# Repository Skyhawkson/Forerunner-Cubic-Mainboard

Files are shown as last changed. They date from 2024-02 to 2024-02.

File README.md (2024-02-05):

# Forerunner-Cubic-Mainboard
**NOTE:** Development prior to Rev1.0.1 occurred in a seperate repository

Forerunner-Cubic-Mainboard-enclosed

Forerunner Cubic is a small form-factor (55 x 55 x ~70mm) flight controller for high-powered rockets and my personal UAV projects. The mainboard uses an ESP32 WROOM-32D module for a processor, and handles data storage, USB, and Single-Pair Ethernet communication with other future devices. The stacking headers enable a connection to other boards handling:
- RF Communication and Control
- Inertial, air data, and environmental sensors
- Servo and pyrotechnic control
- Battery management and power distribution

Design information is available in the [Schematic](https://github.com/Skyhawkson/Forerunner-Cubic-Mainboard/blob/main/Forerunner%20Cubic%20Mainboard%20Rev1.0.1/Forerunner-Cubic-Mainboard.pdf) as well as the [KiCAD 7 Project File](https://github.com/Skyhawkson/Forerunner-Cubic-Mainboard/tree/main/Forerunner%20Cubic%20Mainboard%20Rev1.0.1/Forerunner-Cubic-Mainboard-Rev1.0.1)

The PCB's outer dimensions measure 50 x 50mm, in order to fit within a standard 3" body tube. 

Forerunner_Cubic_PCB

Forerunner_Cubic_Tube

**Board Images:**

Forerunner_Cubic_Bottom
Forerunner_Cubic_Top

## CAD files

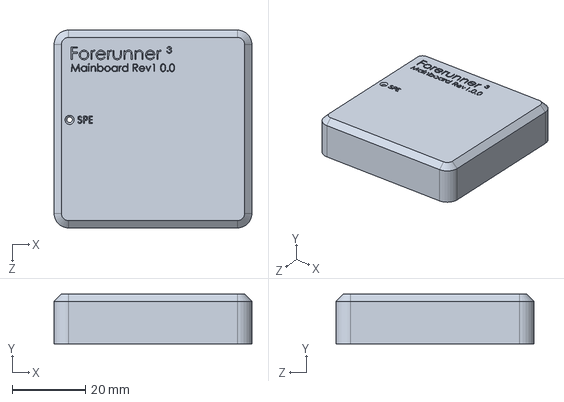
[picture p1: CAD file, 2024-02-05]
Forerunner Cubic Mainboard Rev1.0.1/Bench Test Enclosure/Case Top.SLDPRT
54.0 x 13.6 x 54.0 mm

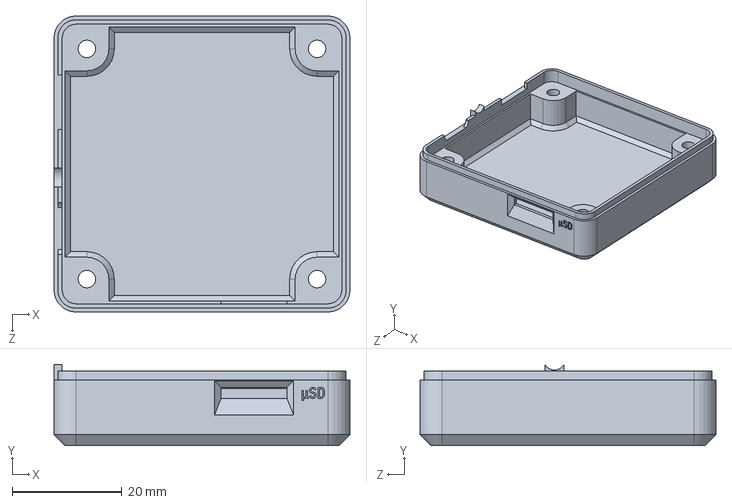
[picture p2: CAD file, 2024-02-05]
Forerunner Cubic Mainboard Rev1.0.1/Bench Test Enclosure/Case Bottom.SLDPRT
54.0 x 14.8 x 54.0 mm

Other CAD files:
Forerunner Cubic Mainboard Rev1.0.1/Bench Test Enclosure/Case Bottom.STL
Forerunner Cubic Mainboard Rev1.0.1/Bench Test Enclosure/Case Top.STL

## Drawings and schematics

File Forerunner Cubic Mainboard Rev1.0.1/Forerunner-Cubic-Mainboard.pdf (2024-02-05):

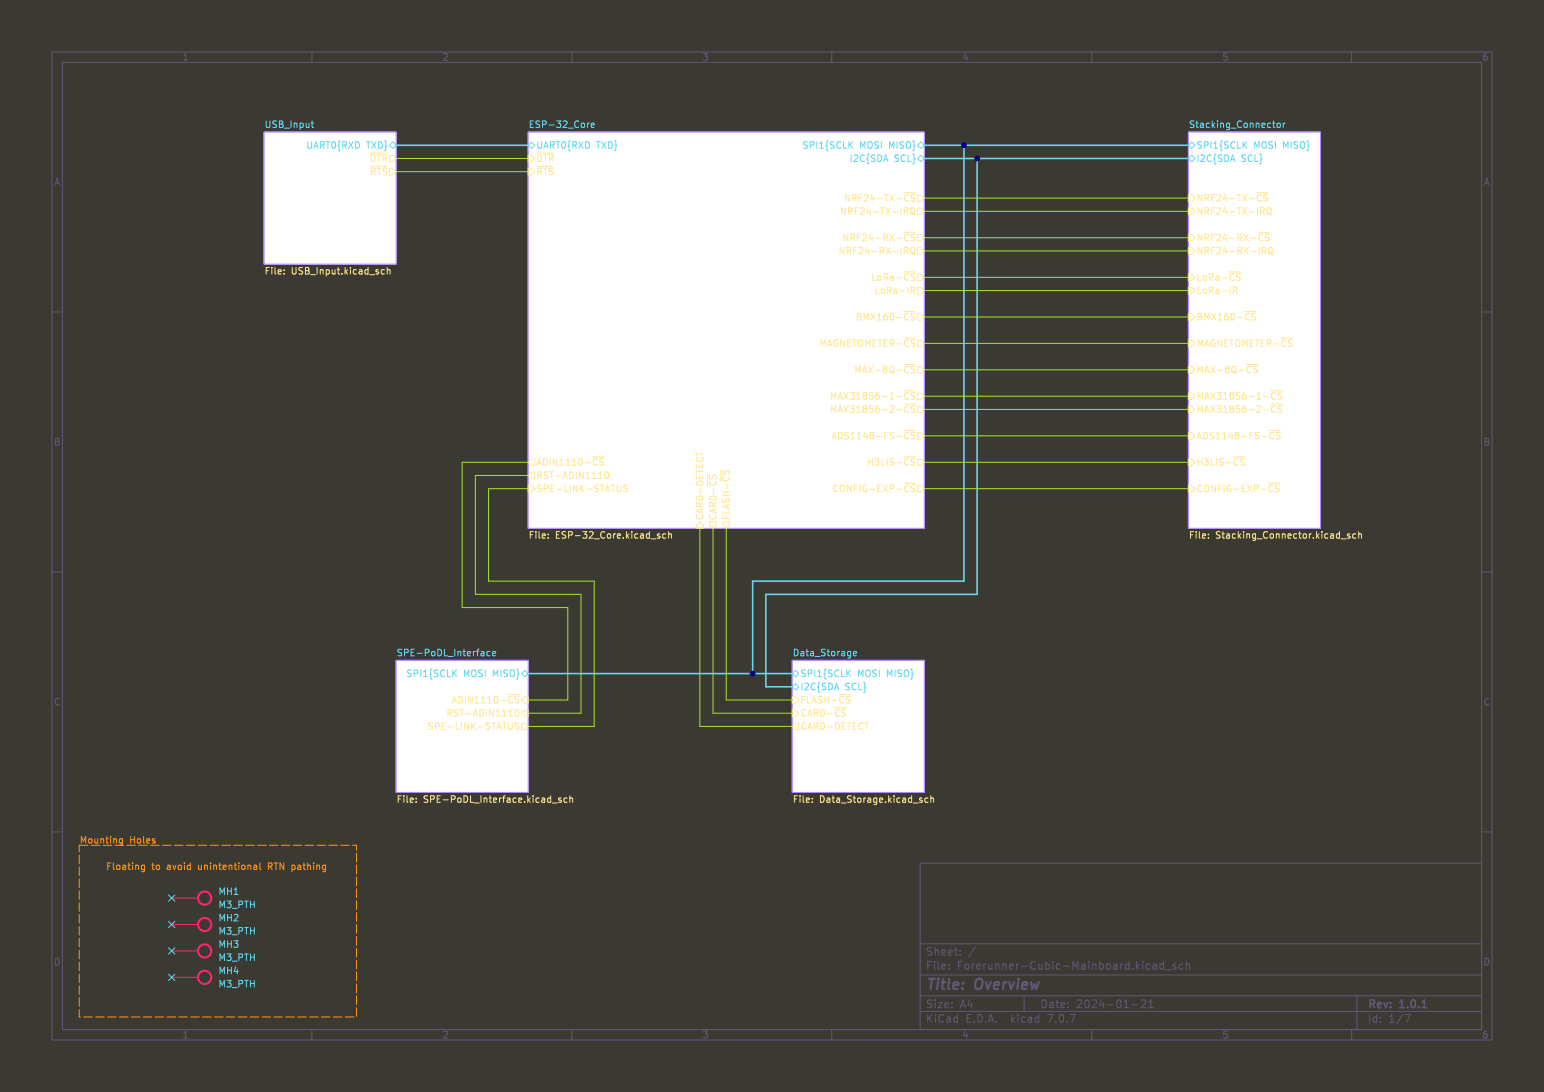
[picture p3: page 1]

NRF24-TX-~{CS} NRF24-RX-IRQ
LoRa-~{CS} NRF24-TX-IRQ

ADIN1110-~{CS} SPE-PoDL_Interface File: SPE-PoDL_Interface.kicad_sch
File: Forerunner-Cubic-Mainboard.kicad_sch Sheet: / SPI1{SCLK MOSI MISO} RST-ADIN1110 SPE-LINK-STATUS

SPI1{SCLK MOSI MISO} CARD-DETECT
I2C{SDA SCL}
FLASH-~{CS}
CARD-~{CS}

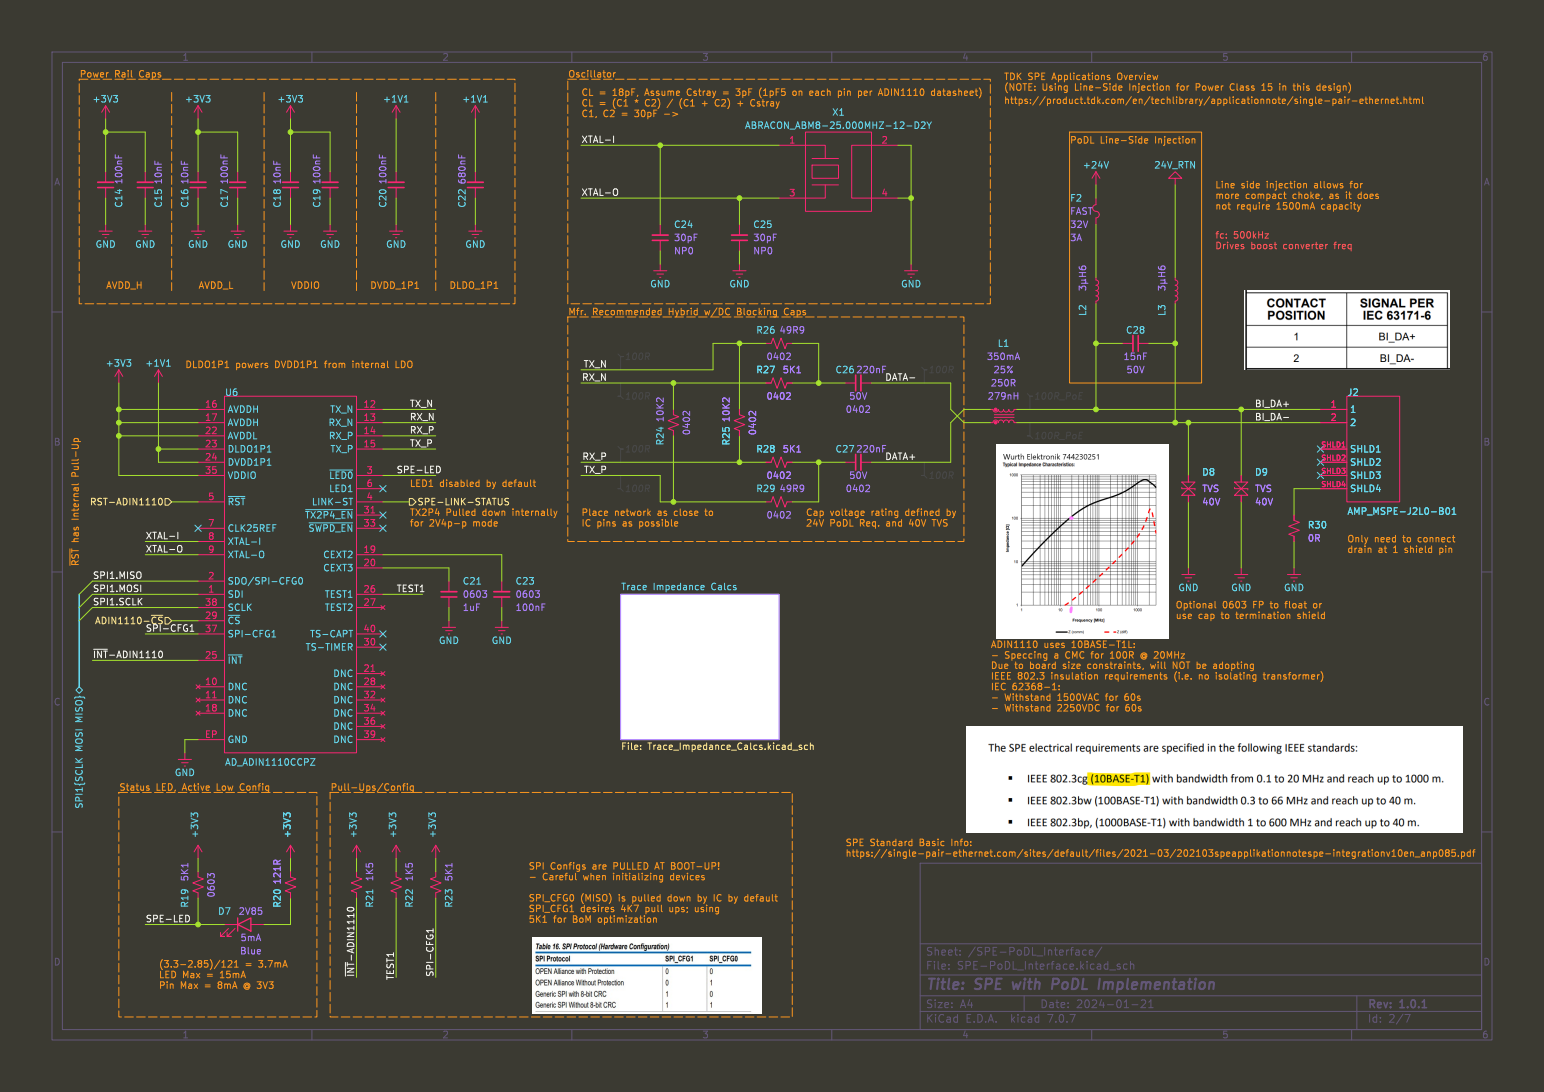
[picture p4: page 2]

Id: 2/7 Title: SPE with PoDL Implementation

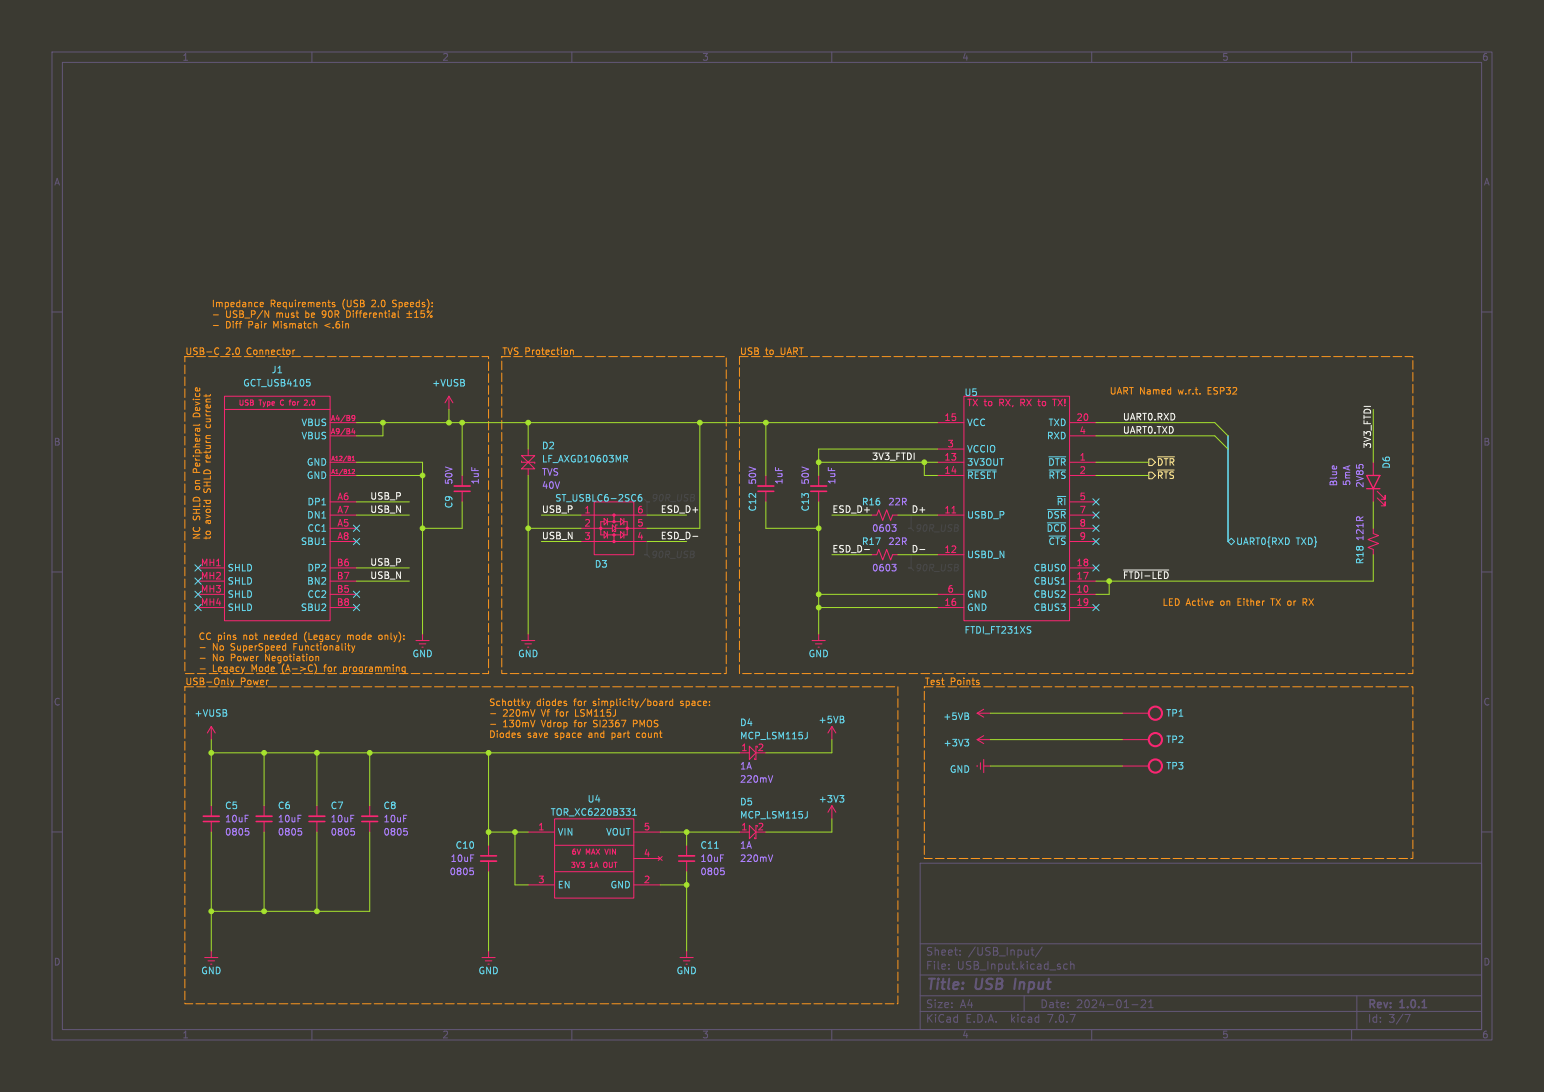
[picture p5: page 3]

Id: 3/7 Title: USB Input File: USB_Input.kicad_sch Sheet: /USB_Input/ R16

- 130mV Vdrop for SI2367 PMOS Diodes save space and part count CC pins not needed (Legacy mode only): - No SuperSpeed Functionality

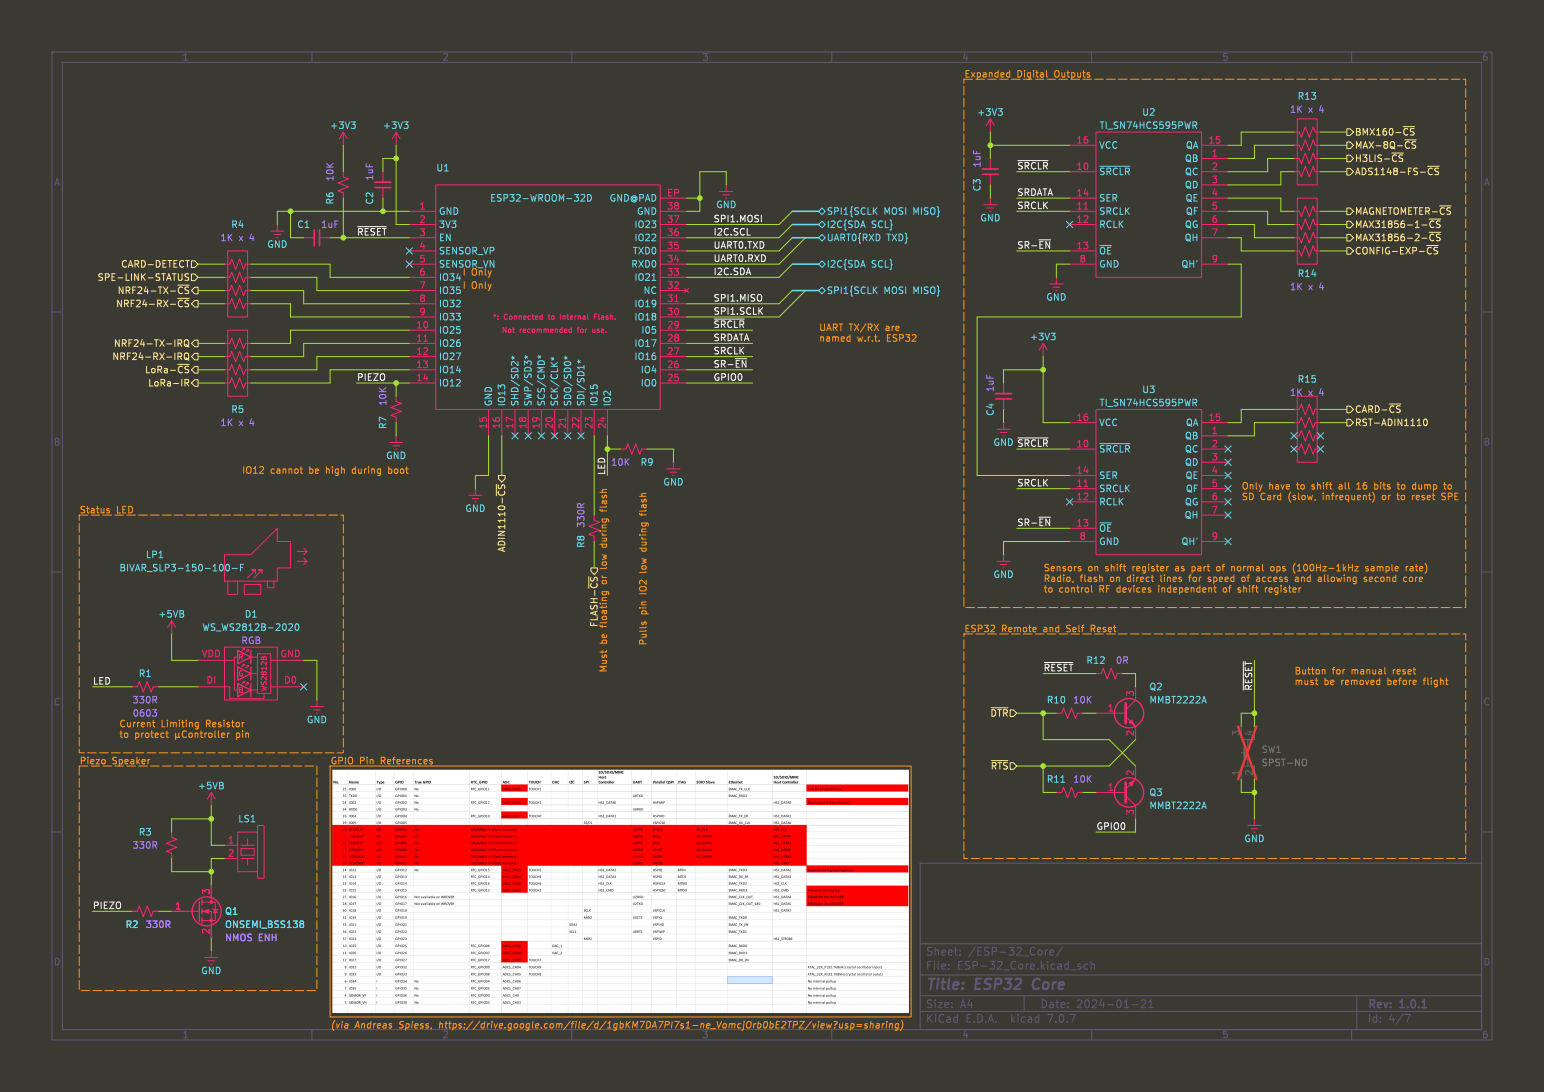
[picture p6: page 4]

CONFIG-EXP-~{CS} FLASH-~{CS}

CARD-DETECT
NRF24-RX-~{CS} SPE-LINK-STATUS NRF24-TX-IRQ
NRF24-TX-~{CS} NRF24-RX-IRQ

(via Andreas Spiess, https://drive.google.com/file/d/1gbKM7DA7PI7s1-ne_VomcjOrb0bE2TPZ/view?usp=sharing) Q1 ONSEMI_BSS138 NMOS ENH

File: ESP-32_Core.kicad_sch Sheet: /ESP-32_Core/
Id: 4/7 Title: ESP32 Core

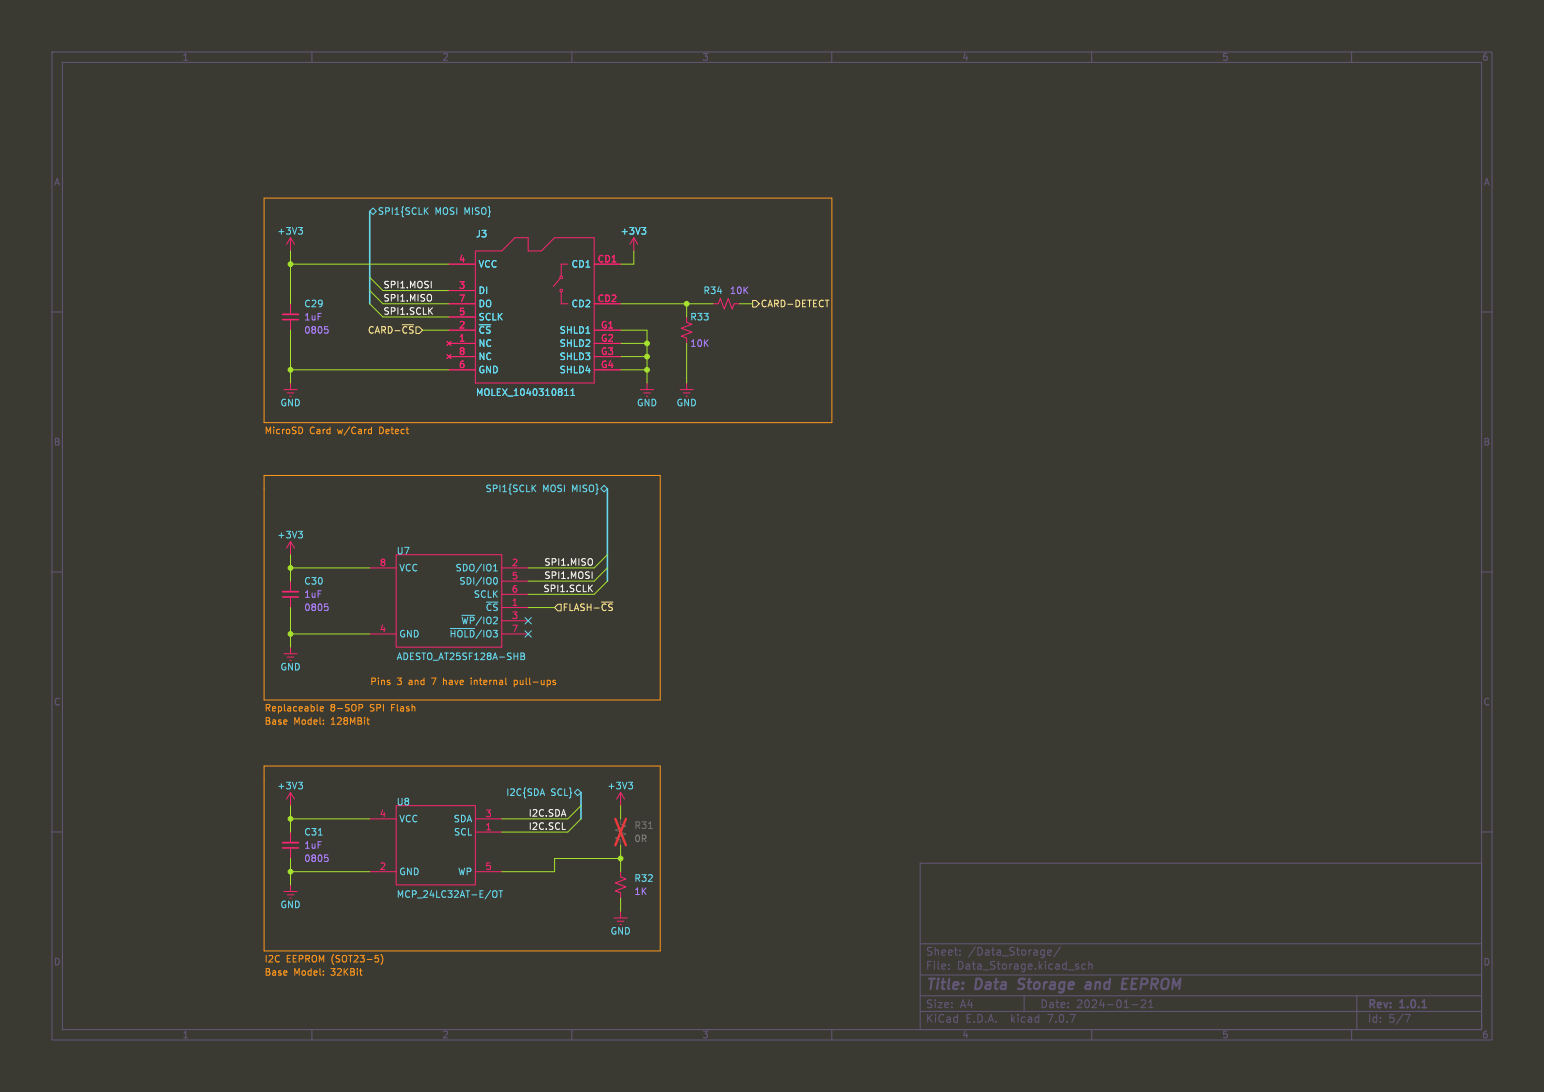
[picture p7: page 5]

File: Data_Storage.kicad_sch Sheet: /Data_Storage/
Id: 5/7 Title: Data Storage and EEPROM

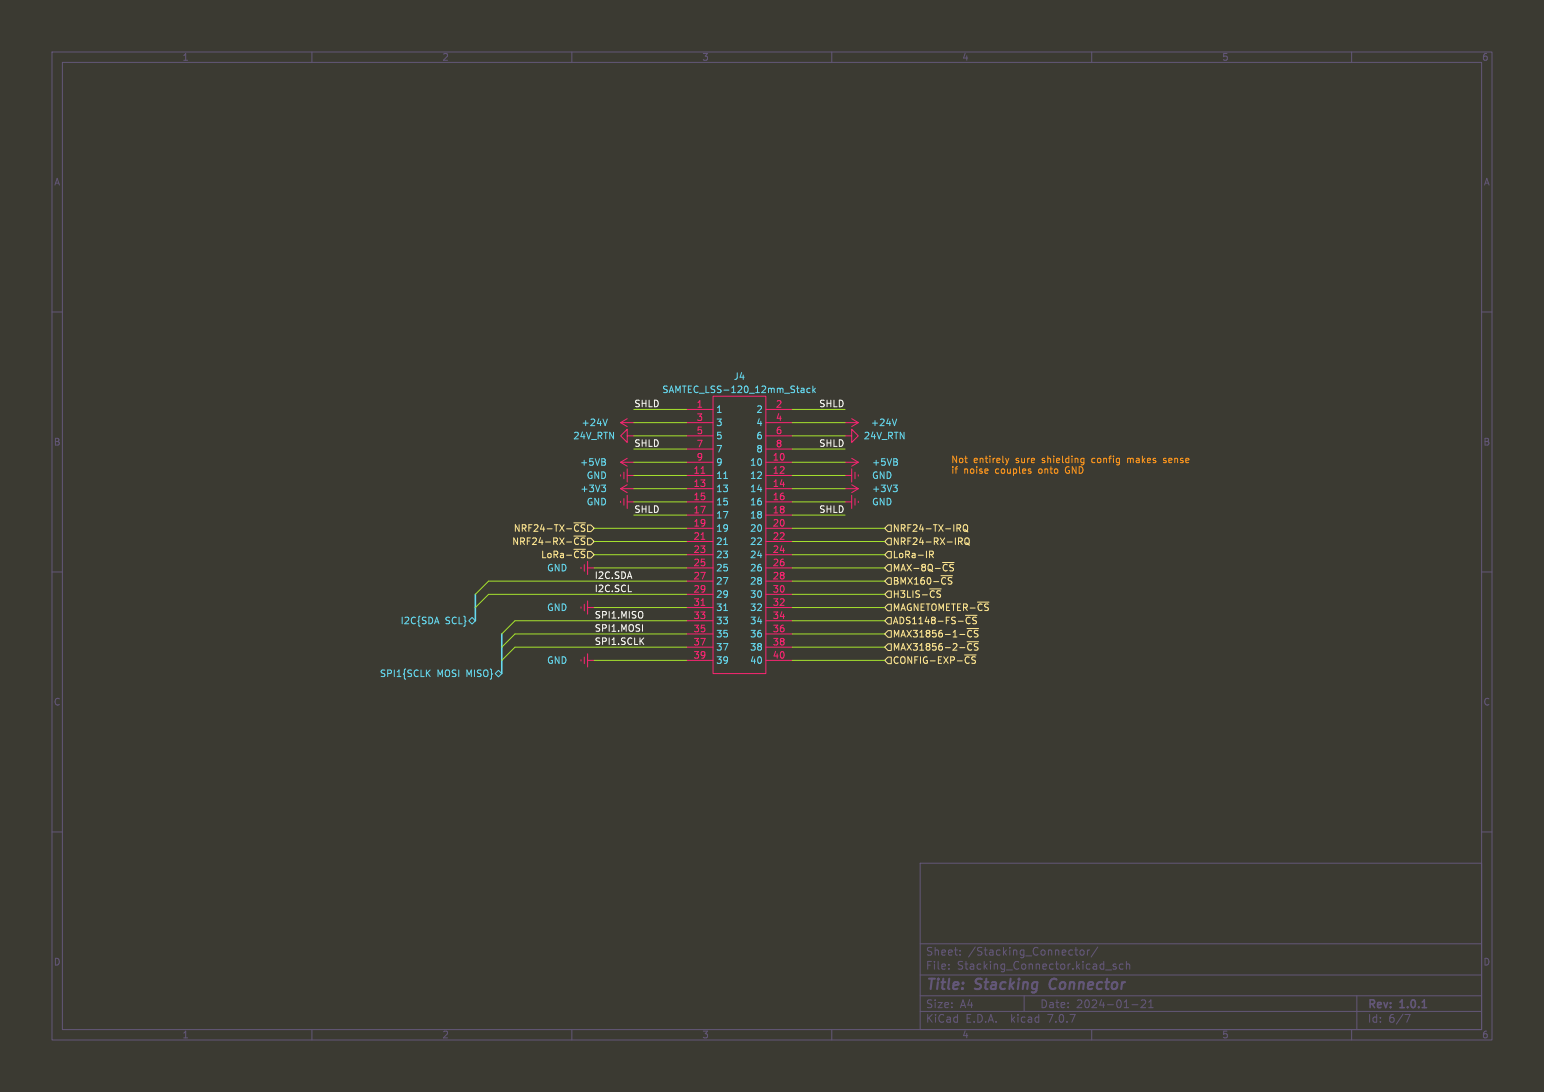
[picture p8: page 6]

if noise couples onto GND

Id: 6/7 Title: Stacking Connector File: Stacking_Connector.kicad_sch Sheet: /Stacking_Connector/

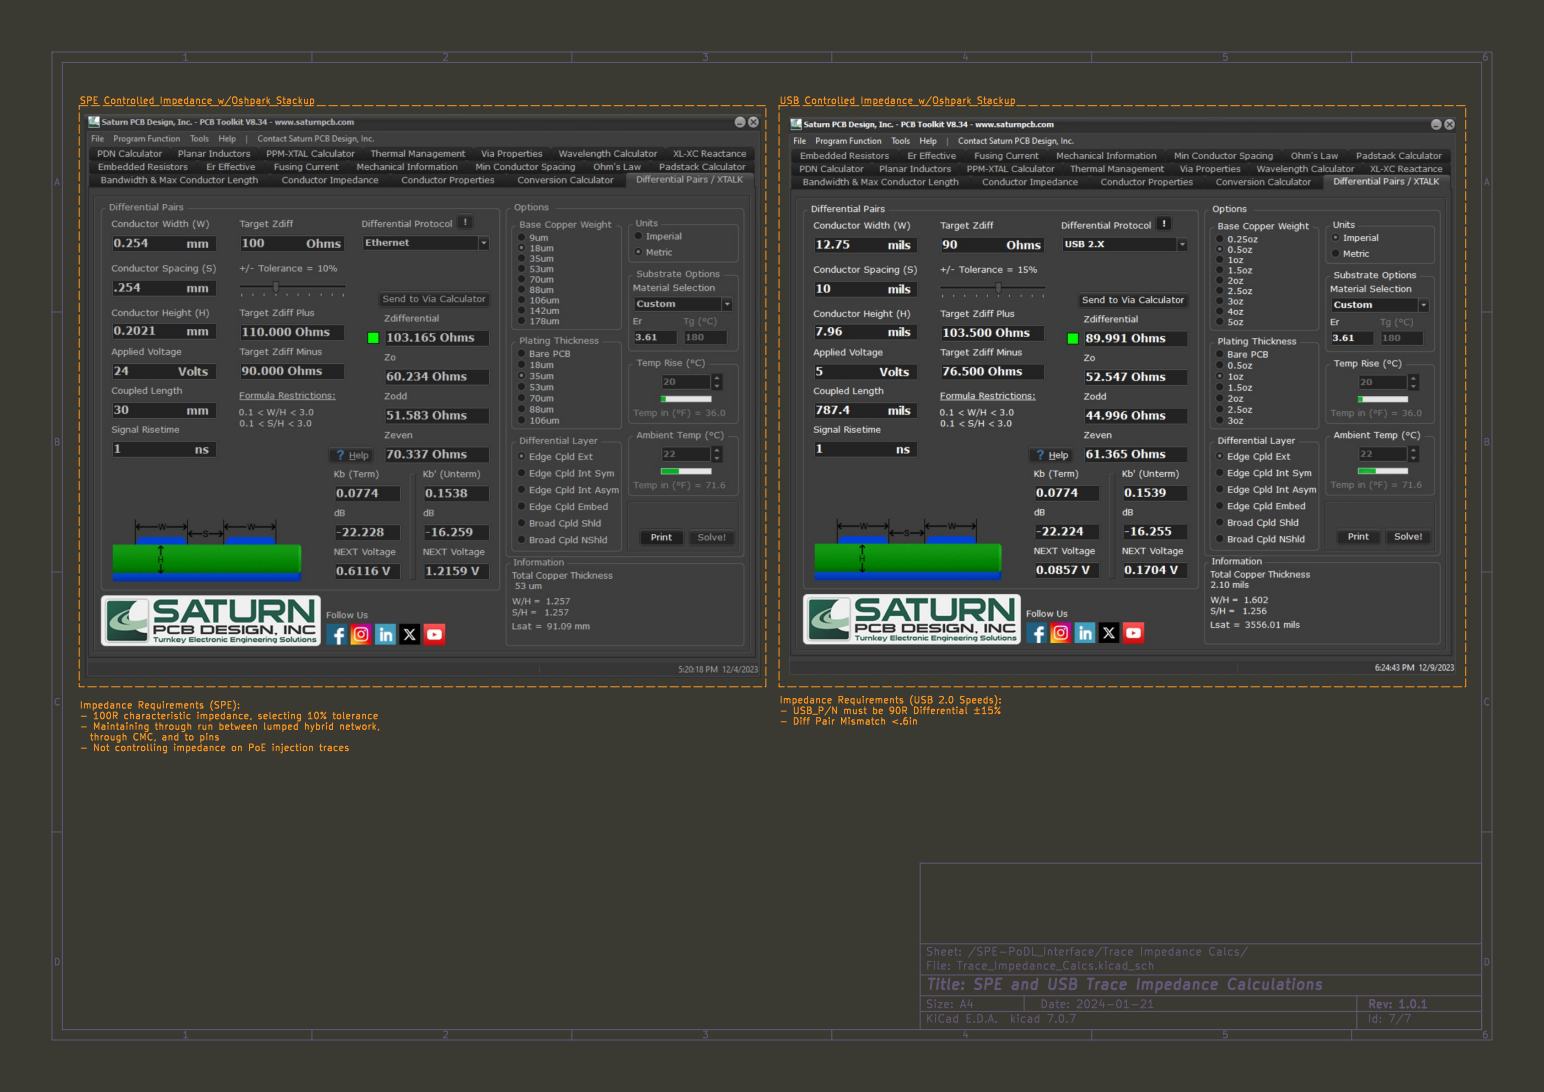
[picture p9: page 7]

through CMC, and to pins

Id: 7/7 Title: SPE and USB Trace Impedance Calculations

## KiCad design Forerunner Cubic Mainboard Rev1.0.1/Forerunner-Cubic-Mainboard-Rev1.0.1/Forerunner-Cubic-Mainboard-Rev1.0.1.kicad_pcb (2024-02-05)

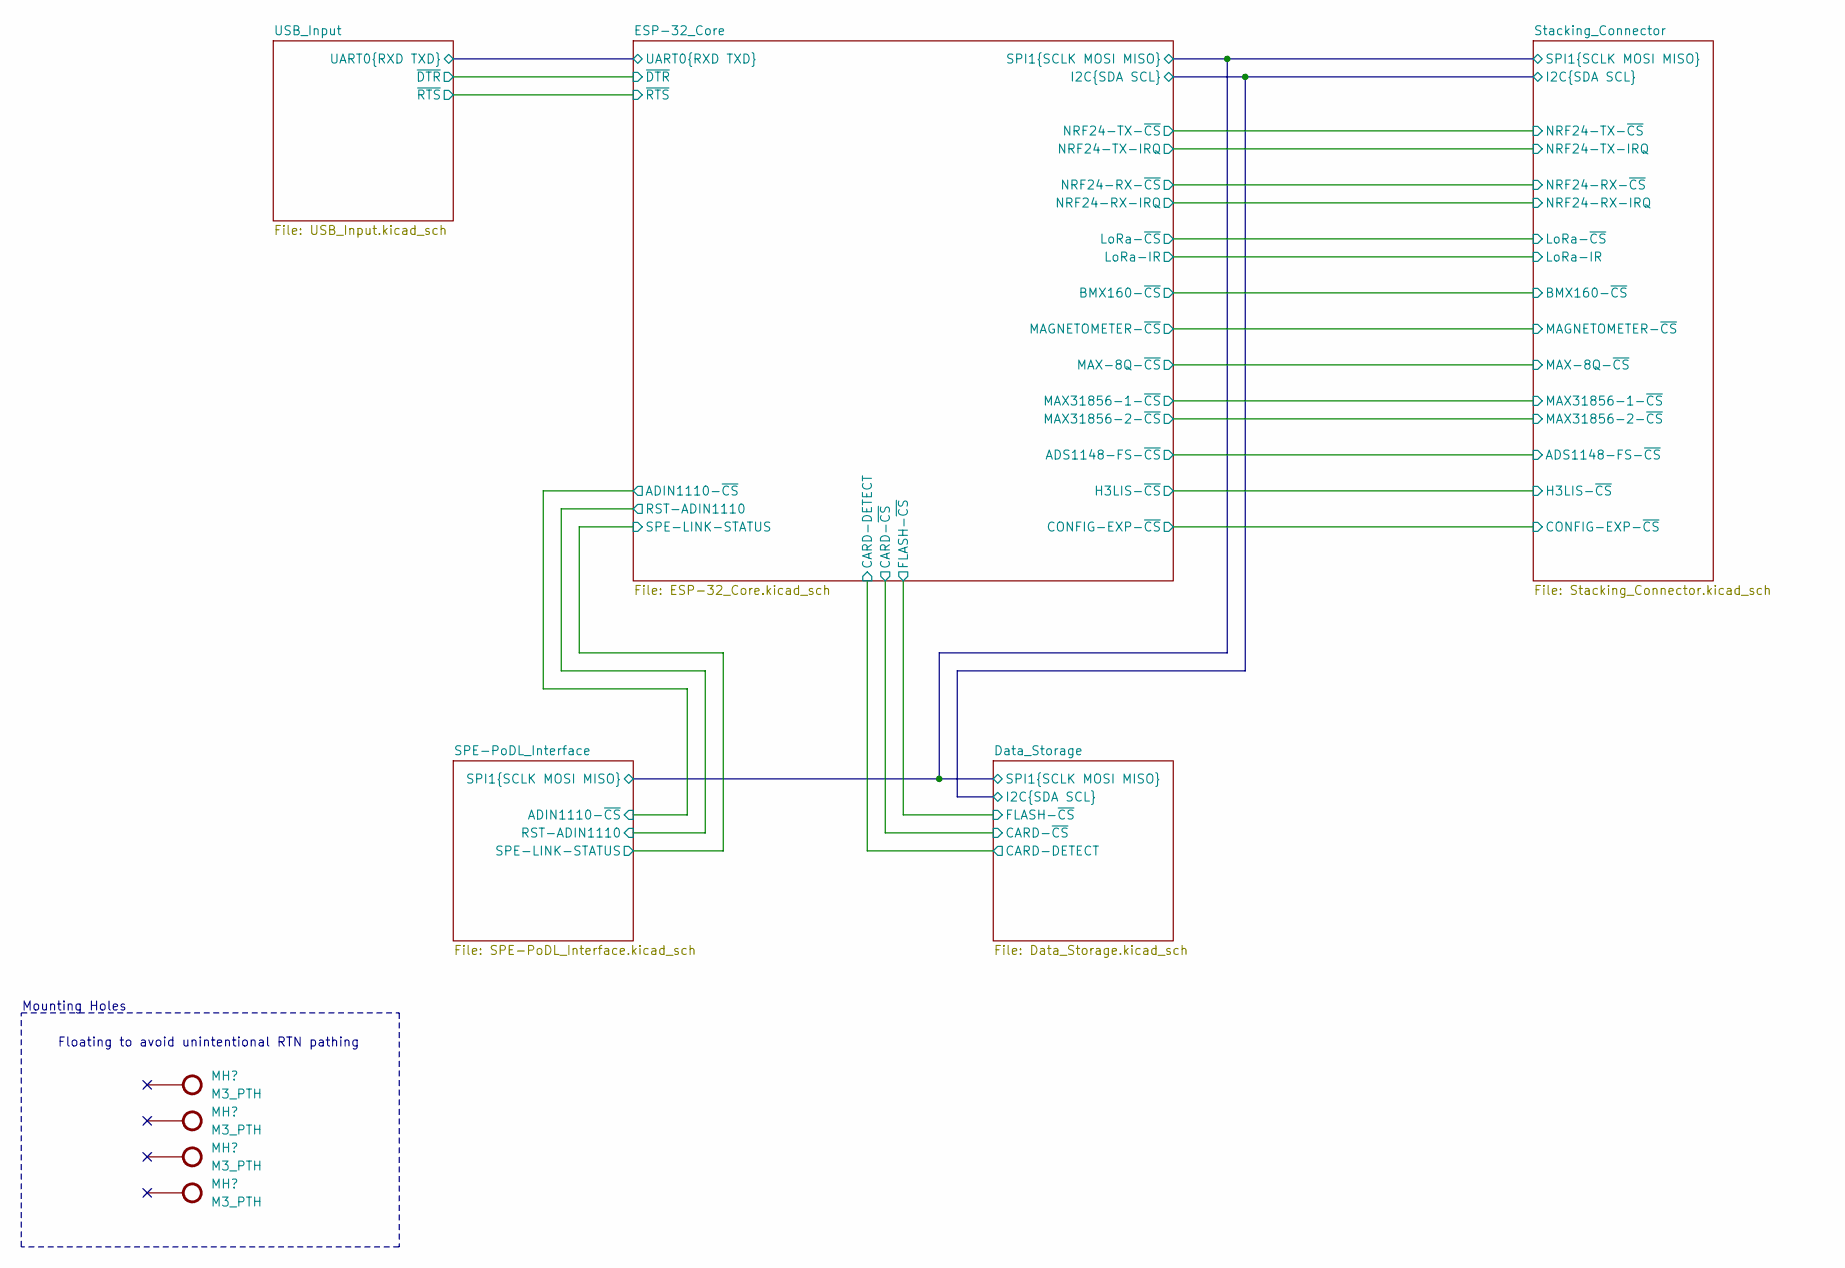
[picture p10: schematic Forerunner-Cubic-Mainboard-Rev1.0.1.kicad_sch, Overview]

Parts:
MH1, MH2, MH3, MH4: M3_PTH; GENERIC_MH_M3

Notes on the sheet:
Mounting Holes
Floating to avoid unintentional RTN pathing

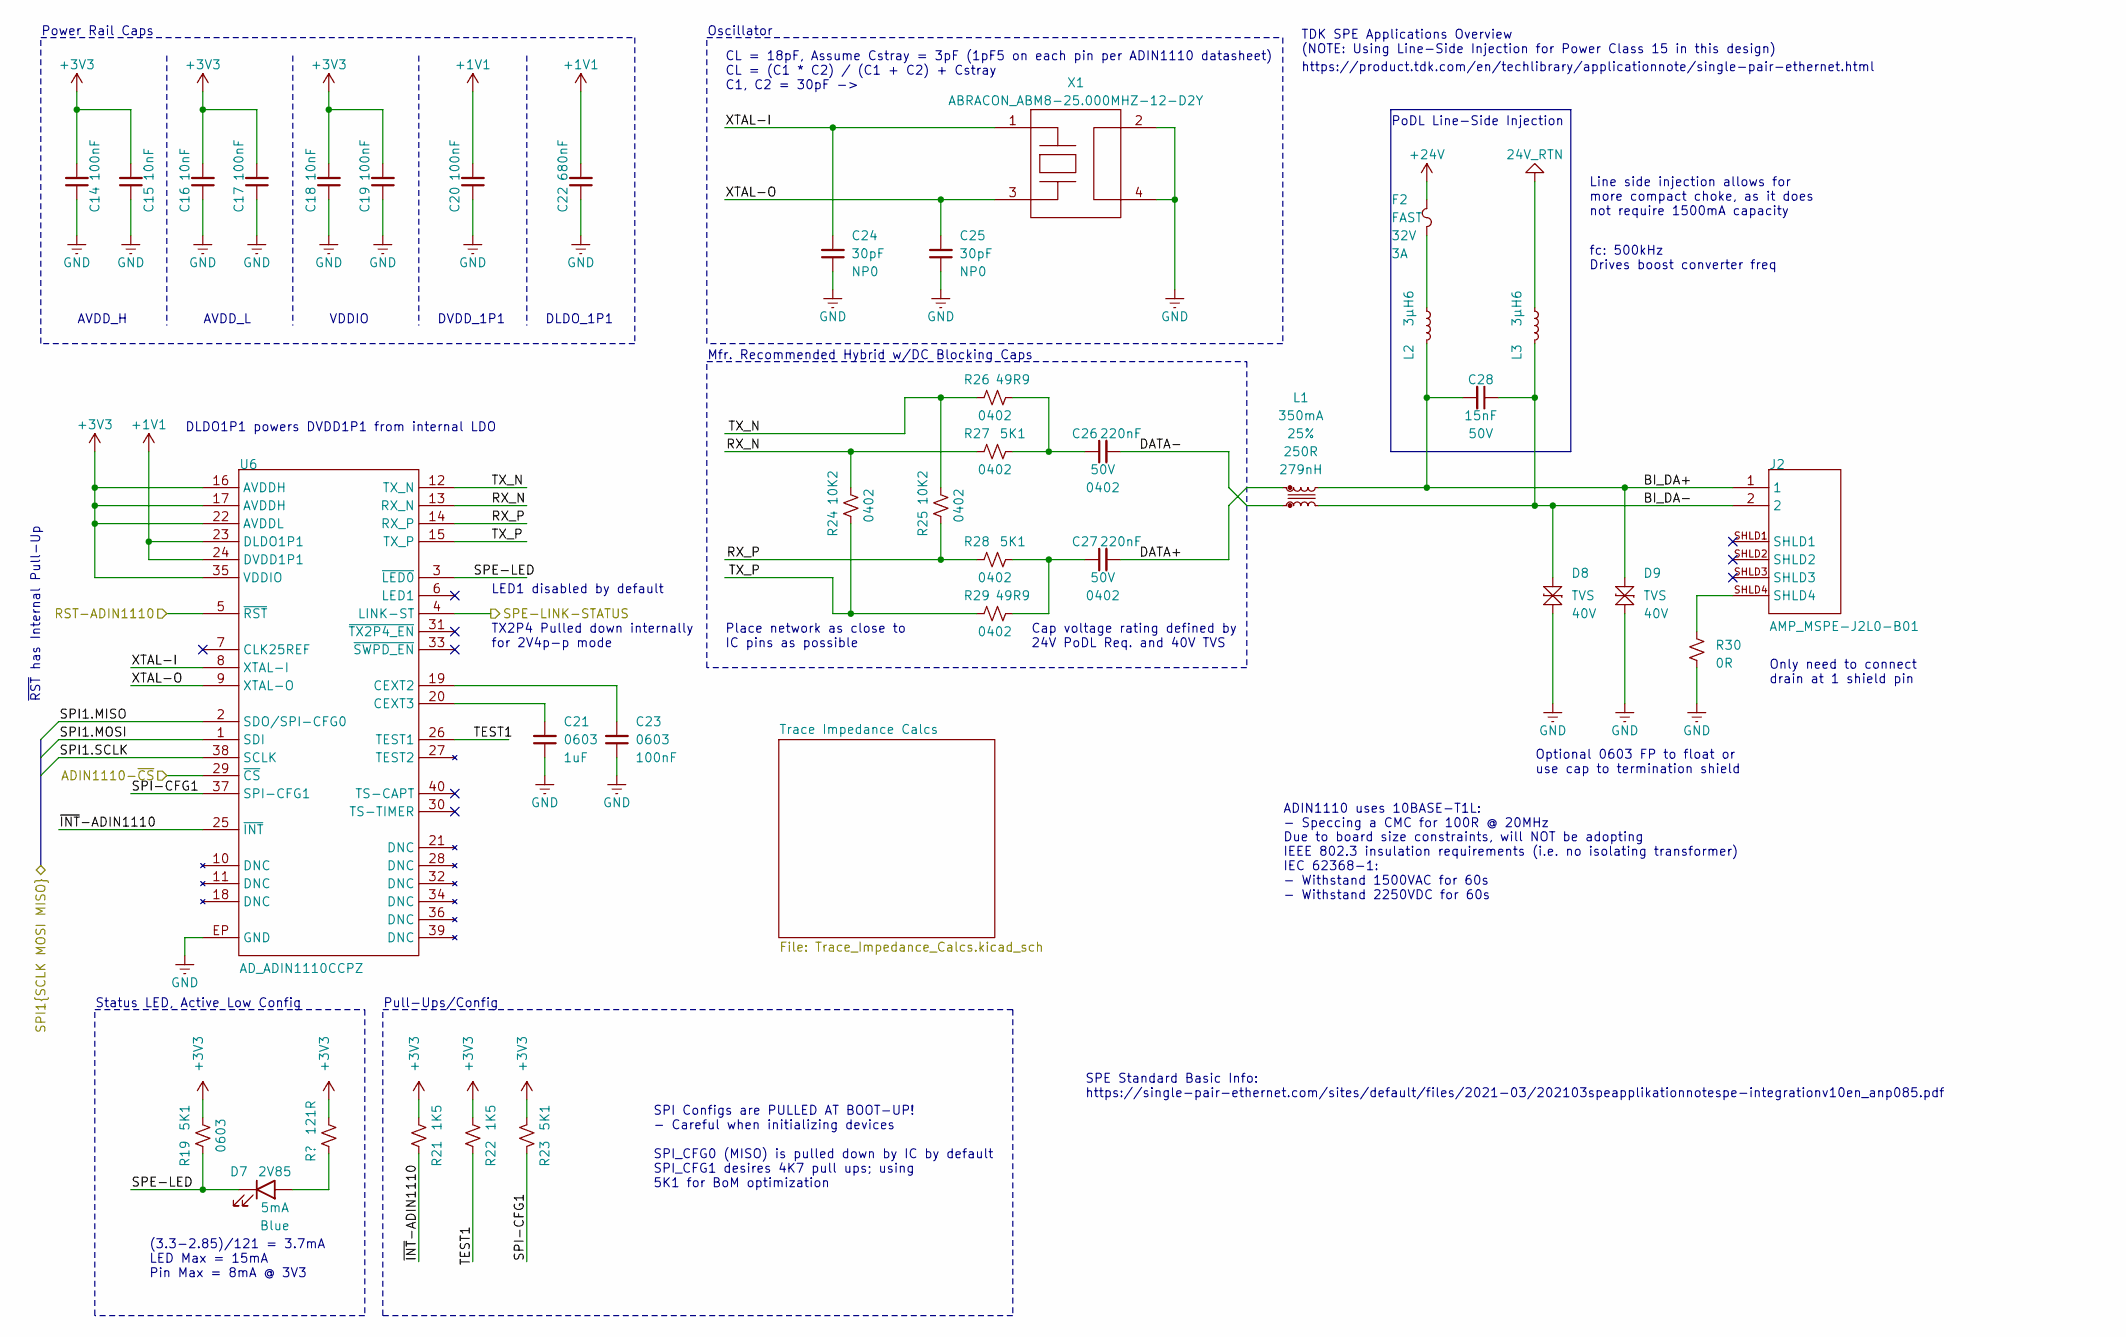
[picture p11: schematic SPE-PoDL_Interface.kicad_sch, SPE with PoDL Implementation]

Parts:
C14, C17, C19, C20, C23: 100NF_0603; GENERIC_0603_CAP; Tolerance 10%; Rating 25V
C15, C16, C18: 10NF_0603; GENERIC_0603_CAP; Tolerance 10%; Rating 25V
C21: 1UF_0603; GENERIC_0603_CAP; Tolerance 10%; Rating 25V
C22: 680NF_0603; GENERIC_0603_CAP; Tolerance 20%; Rating 25V
C24, C25: 30PF_0603; GENERIC_0603_CAP; Tolerance 10%; Rating 50V
C26, C27: 220NF_0402; GENERIC_0402_CAP; Tolerance 10%; Rating 50V
C28: 15NF_0603; GENERIC_0603_CAP; Tolerance 10%; Rating 50V
D7: OSRAM_LBQ39E-N1OO-35-1; OSRAM_0603
D8, D9: LF_AXGD10603MR; LF_AXGD1_0603
F2: LF_0494003; LF_0494_(0603); VOLTAGE 32V
J2: AMP_MSPE-J2L0-B01
L1: WE_744230251; WE_CNSW-0603; Tolerance 25%
L2, L3: BOURNS_SRP5030TA-3R6M; BOURNS_SRP5030TA; Tolerance 20%
R19, R23: 5K1_0603; GENERIC_0603_RES; Tolerance 1%
R20: 121R_0603; GENERIC_0603_RES; Tolerance 1%
R21, R22: 1K5_0603; GENERIC_0603_RES; Tolerance 1%
R24, R25: 10K2_0402; GENERIC_0402_RES; Tolerance 1%
R26, R29: 49R9_0402; GENERIC_0402_RES; Tolerance 1%
R27, R28: 5K1_0402; GENERIC_0402_RES; Tolerance 1%
R30: 0R_0603; GENERIC_0603_RES; Tolerance 1%
U6: AD_ADIN1110CCPZ; AD_ADIN1110
X1: ABRACON_ABM8-25.000MHZ-12-D2Y; ABRACON_ABM8

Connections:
24V_RTN: L3.1; also elsewhere on the board
+1V1: C20.2, C22.2, U6.23 (DLDO1P1), U6.24 (DVDD1P1)
+3V3: C14.2, C15.2, C16.2, C17.2, C18.2, C19.2, R19.2, R20.2, R21.2, R22.2, R23.2, U6.16 (AVDDH), U6.17 (AVDDH), U6.22 (AVDDL), U6.35 (VDDIO); also elsewhere on the board
+24V: F2.2; also elsewhere on the board
/Data_Storage/SPI1.MISO: U6.2 (SDO/SPI-CFG0); also elsewhere on the board
/Data_Storage/SPI1.MOSI: U6.1 (SDI); also elsewhere on the board
/Data_Storage/SPI1.SCLK: U6.38 (SCLK); also elsewhere on the board
/ESP-32_Core/ADIN1110-~CS: U6.29 (~CS); also elsewhere on the board
/ESP-32_Core/RST-ADIN1110: U6.5 (~RST); also elsewhere on the board
/ESP-32_Core/SPE-LINK-STATUS: U6.4 (LINK-ST); also elsewhere on the board
/SPE-PoDL_Interface/BI_DA+: C28.2, D9.2, J2.1, L1.2, L2.2
/SPE-PoDL_Interface/BI_DA-: C28.1, D8.2, J2.2, L1.3, L3.2
/SPE-PoDL_Interface/DATA+: C27.2, L1.1
/SPE-PoDL_Interface/DATA-: C26.2, L1.4
/SPE-PoDL_Interface/RX_N: R24.2, R27.1, U6.13 (RX_N)
/SPE-PoDL_Interface/RX_P: R25.1, R28.1, U6.14 (RX_P)
/SPE-PoDL_Interface/SPE-LED: D7.C, R19.1, U6.3 (~LED0)
/SPE-PoDL_Interface/SPI-CFG1: R23.1, U6.37 (SPI-CFG1)
/SPE-PoDL_Interface/TEST1: R22.1, U6.26 (TEST1)
/SPE-PoDL_Interface/TX_N: R25.2, R26.1, U6.12 (TX_N)
/SPE-PoDL_Interface/TX_P: R24.1, R29.1, U6.15 (TX_P)
/SPE-PoDL_Interface/XTAL-I: C24.2, U6.8 (XTAL-I), X1.1
/SPE-PoDL_Interface/XTAL-O: C25.2, U6.9 (XTAL-O), X1.3
/SPE-PoDL_Interface/~INT-ADIN1110: R21.1, U6.25 (~INT)
GND: C14.1, C15.1, C16.1, C17.1, C18.1, C19.1, C20.1, C21.1, C22.1, C23.1, C24.1, C25.1, D8.1, D9.1, R30.1, U6.EP (GND), X1.2, X1.4; also elsewhere on the board
unnamed: C26.1, R26.2, R27.2
unnamed: C27.1, R28.2, R29.2
unnamed: D7.A, R20.1
unnamed: F2.1, L2.1
unnamed: J2.SHLD4, R30.2
unnamed: C23.2, U6.19 (CEXT2)
unnamed: C21.2, U6.20 (CEXT3)

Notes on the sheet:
DLDO1P1 powers DVDD1P1 from internal LDO
Oscillator
DLDO_1P1
LED1 disabled by default
ADIN1110 uses 10BASE-T1L: - Speccing a CMC for 100R @ 20MHz
https://product.tdk.com/en/techlibrary/applicationnote/single-pair-ethernet.html
SPI Configs are PULLED AT BOOT-UP! - Careful when initializing devices SPI_CFG0 (MISO) is pulled down by IC by default SPI_CFG1 desires 4K7 pull ups; using 5K1 for BoM optimization
Place network as close to IC pins as possible
Due to board size constraints, will NOT be adopting IEEE 802.3 insulation requirements (i.e. no isolating transformer) IEC 62368-1: - Withstand 1500VAC for 60s - Withstand 2250VDC for 60s
(3.3-2.85)/121 = 3.7mA LED Max = 15mA Pin Max = 8mA @ 3V3
PoDL Line-Side Injection
Line side injection allows for more compact choke, as it does not require 1500mA capacity
fc: 500kHz Drives boost converter freq
Status LED, Active Low Config
TDK SPE Applications Overview (NOTE: Using Line-Side Injection for Power Class 15 in this design)
TX2P4 Pulled down internally for 2V4p-p mode
Power Rail Caps
SPE Standard Basic Info: https://single-pair-ethernet.com/sites/default/files/2021-03/202103speapplikationnotespe-integrationv10en_anp085.pdf
Cap voltage rating defined by 24V PoDL Req. and 40V TVS
Pull-Ups/Config
VDDIO
AVDD_H
AVDD_L
Optional 0603 FP to float or use cap to termination shield
DVDD_1P1
Mfr. Recommended Hybrid w/DC Blocking Caps
~{RST} has Internal Pull-Up
Only need to connect drain at 1 shield pin
CL = 18pF, Assume Cstray = 3pF (1pF5 on each pin per ADIN1110 datasheet) CL = (C1 * C2) / (C1 + C2) + Cstray C1, C2 = 30pF ->

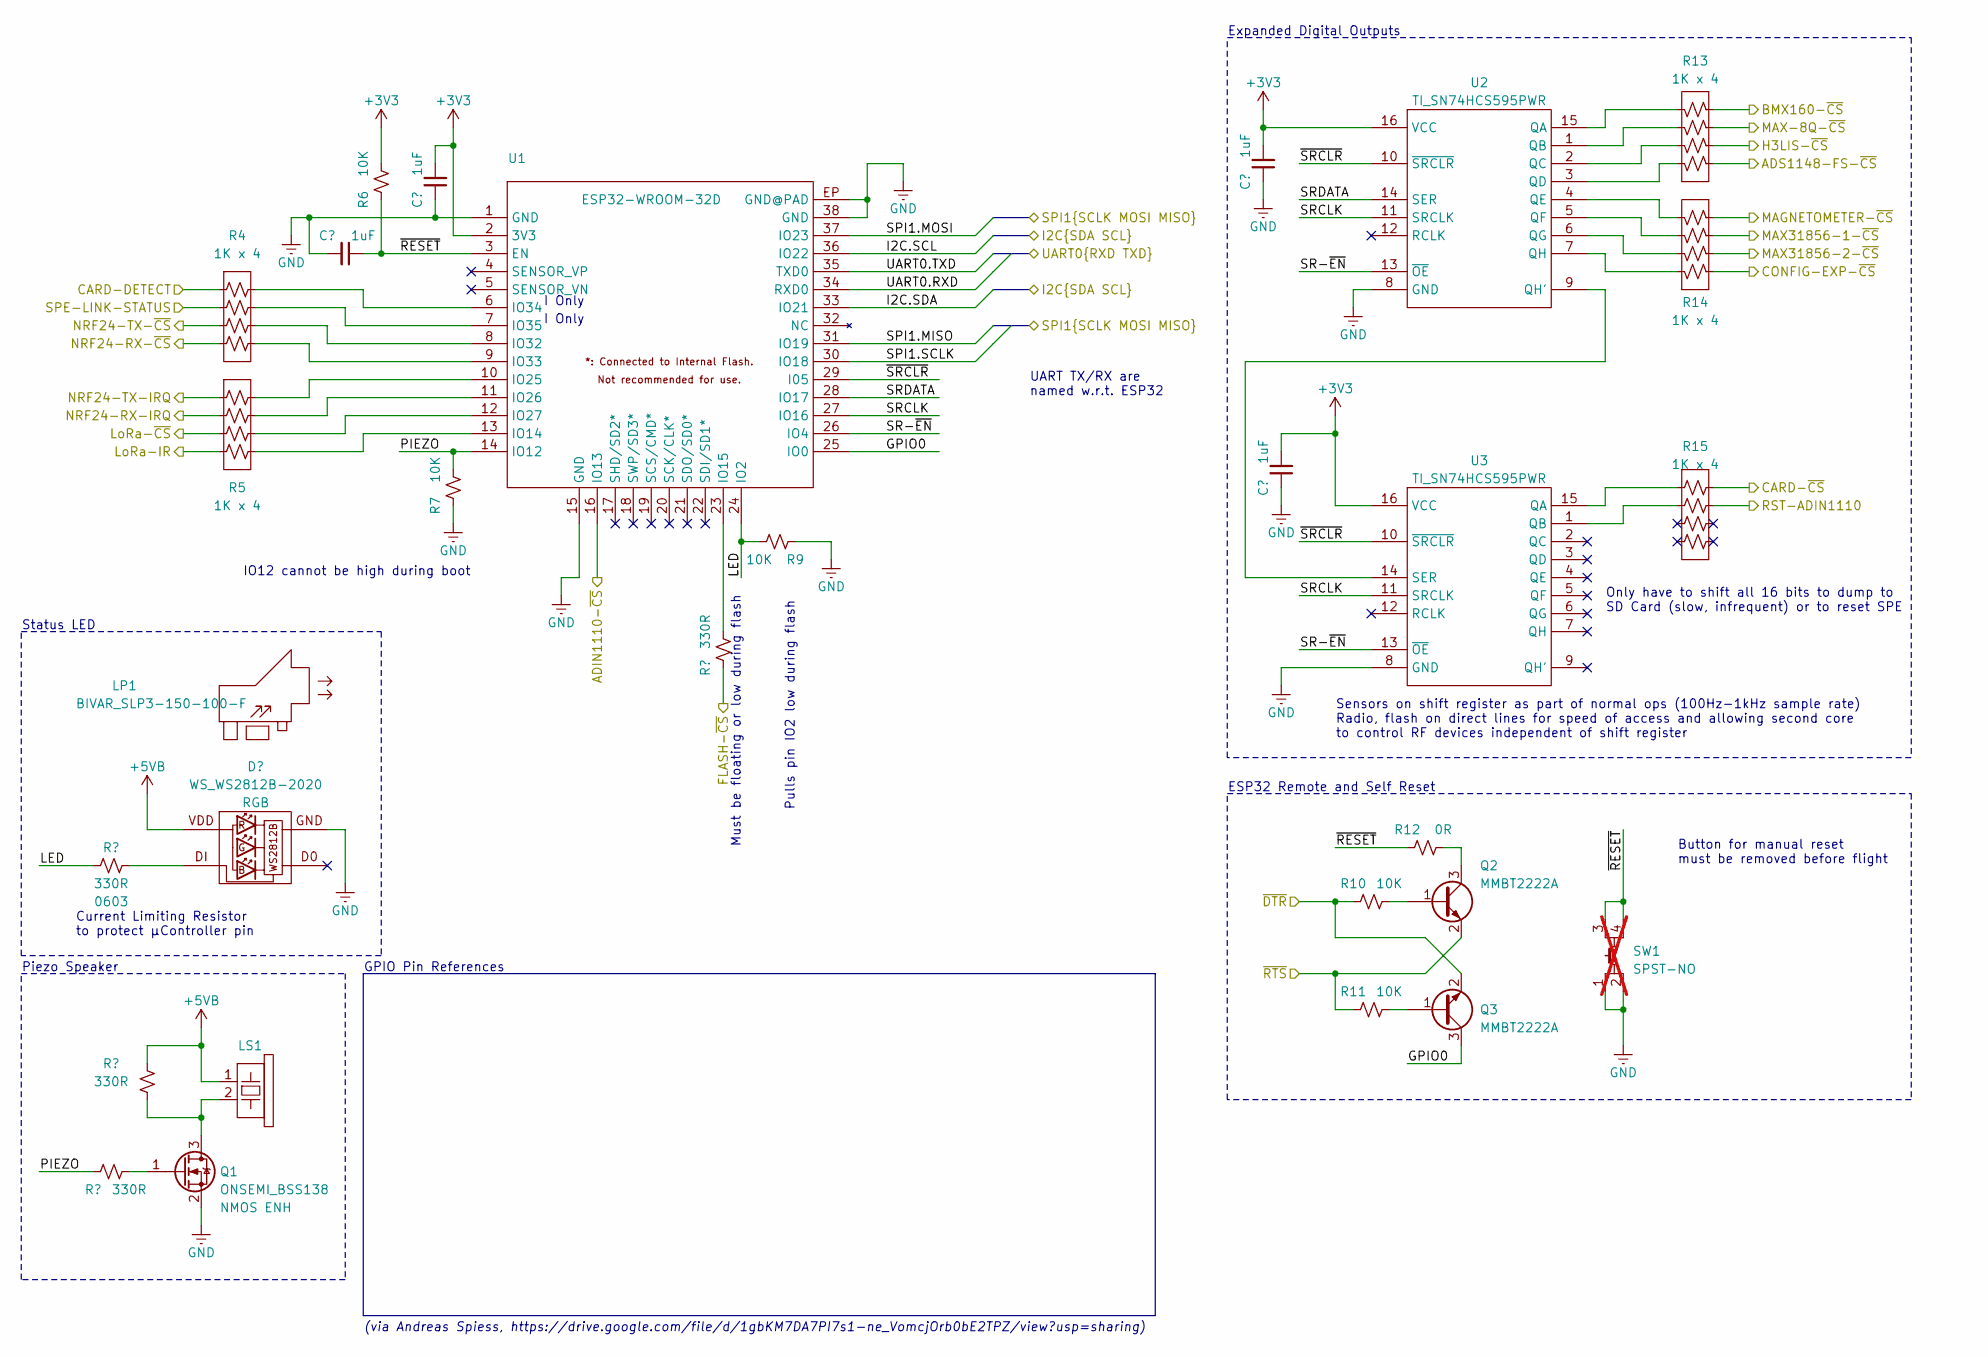
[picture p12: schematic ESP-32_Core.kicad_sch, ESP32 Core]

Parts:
C1, C2, C3, C4: 1UF_0805; GENERIC_0805_CAP; Tolerance 10%; Rating 50V
D1: WS_WS2812B-2020
LP1: BIVAR_SLP3-150-100-F
LS1: MURATA_PKMCS0909E4000-R1; MURATA_PKMCS
Q1: ONSEMI_BSS138; GENERIC_SOT-23
Q2, Q3: MMBT2222A; GENERIC_SOT-23
R1, R2, R3, R8: 1K33_0603; GENERIC_0603_RES; Tolerance 1%
R4, R5, R13, R14, R15: CAT16-1001F4LF; BOURNS_CAT16-X4; Tolerance 1%
R6, R7, R9, R10, R11: 10K_0603; GENERIC_0603_RES; Tolerance 1%
R12: 0R_0603; GENERIC_0603_RES; Tolerance 1%
SW1: CK_PTS815-SJG-250-XXXX-LFS; CK_PTS815; not fitted
U1: ESP32-WROOM-32D; ESPRESSIF_ESP-WROOM-32D
U2, U3: TI_SN74HCS595PWR; TI_PW0016A_(TSSOP-16)

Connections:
+3V3: C2.2, C3.2, C4.2, R6.2, U1.2 (3V3), U2.16 (VCC), U3.16 (VCC); also elsewhere on the board
+5VB: D1.4 (VDD), LS1.1, R3.2; also elsewhere on the board
/Data_Storage/CARD-DETECT: R4.1; also elsewhere on the board
/Data_Storage/CARD-~CS: R15.8; also elsewhere on the board
/Data_Storage/FLASH-~CS: R8.1; also elsewhere on the board
/Data_Storage/I2C.SCL: U1.36 (IO22); also elsewhere on the board
/Data_Storage/I2C.SDA: U1.33 (IO21); also elsewhere on the board
/Data_Storage/SPI1.MISO: U1.31 (IO19); also elsewhere on the board
/Data_Storage/SPI1.MOSI: U1.37 (IO23); also elsewhere on the board
/Data_Storage/SPI1.SCLK: U1.30 (IO18); also elsewhere on the board
/ESP-32_Core/ADIN1110-~CS: U1.16 (IO13); also elsewhere on the board
/ESP-32_Core/ADS1148-FS-~CS: R13.8; also elsewhere on the board
/ESP-32_Core/BMX160-~CS: R13.5; also elsewhere on the board
/ESP-32_Core/CONFIG-EXP-~CS: R14.8; also elsewhere on the board
/ESP-32_Core/GPIO0: Q3.3 (C), U1.25 (IO0)
/ESP-32_Core/H3LIS-~CS: R13.7; also elsewhere on the board
/ESP-32_Core/LED: R1.1, R9.2, U1.24 (IO2)
/ESP-32_Core/LoRa-IR: R5.4; also elsewhere on the board
/ESP-32_Core/LoRa-~CS: R5.3; also elsewhere on the board
/ESP-32_Core/MAGNETOMETER-~CS: R14.5; also elsewhere on the board
/ESP-32_Core/MAX31856-1-~CS: R14.6; also elsewhere on the board
/ESP-32_Core/MAX31856-2-~CS: R14.7; also elsewhere on the board
/ESP-32_Core/MAX-8Q-~CS: R13.6; also elsewhere on the board
/ESP-32_Core/NRF24-RX-IRQ: R5.2; also elsewhere on the board
/ESP-32_Core/NRF24-RX-~CS: R4.4; also elsewhere on the board
/ESP-32_Core/NRF24-TX-IRQ: R5.1; also elsewhere on the board
/ESP-32_Core/NRF24-TX-~CS: R4.3; also elsewhere on the board
/ESP-32_Core/PIEZO: R2.1, R7.2, U1.14 (IO12)
/ESP-32_Core/RST-ADIN1110: R15.7; also elsewhere on the board
/ESP-32_Core/SPE-LINK-STATUS: R4.2; also elsewhere on the board
/ESP-32_Core/SR-~EN: U1.26 (IO4), U2.13 (~OE), U3.13 (~OE)
/ESP-32_Core/SRCLK: U1.27 (IO16), U2.11 (SRCLK), U3.11 (SRCLK)
/ESP-32_Core/SRDATA: U1.28 (IO17), U2.14 (SER)
/ESP-32_Core/UART0.RXD: U1.34 (RXD0); also elsewhere on the board
/ESP-32_Core/UART0.TXD: U1.35 (TXD0); also elsewhere on the board
/ESP-32_Core/~DTR: Q3.2 (E), R10.1; also elsewhere on the board
/ESP-32_Core/~RESET: C1.1, R6.1, R12.1, SW1.3, SW1.4, U1.3 (EN)
/ESP-32_Core/~RTS: Q2.2 (E), R11.1; also elsewhere on the board
/ESP-32_Core/~SRCLR: U1.29 (I05), U2.10 (~SRCLR), U3.10 (~SRCLR)
GND: C1.2, C2.1, C3.1, C4.1, D1.2 (GND), Q1.2 (S), R7.1, R9.1, SW1.1, SW1.2, U1.1 (GND), U1.15 (GND), U1.38 (GND), U1.EP (GND@PAD), U2.8 (GND), U3.8 (GND); also elsewhere on the board
unnamed: D1.3 (DI), R1.2
unnamed: LS1.2, Q1.3 (D), R3.1
unnamed: Q1.1 (G), R2.2
unnamed: Q2.1 (B), R10.2
unnamed: Q2.3 (C), R12.2
unnamed: Q3.1 (B), R11.2
unnamed: R5.5, U1.13 (IO14)
unnamed: R8.2, U1.23 (IO15)
unnamed: R5.8, U1.10 (IO25)
unnamed: R5.7, U1.11 (IO26)
unnamed: R5.6, U1.12 (IO27)
unnamed: R4.6, U1.8 (IO32)
unnamed: R4.5, U1.9 (IO33)
unnamed: R4.8, U1.6 (IO34)
unnamed: R4.7, U1.7 (IO35)
unnamed: R13.4, U2.15 (QA)
unnamed: R13.3, U2.1 (QB)
unnamed: R13.2, U2.2 (QC)
unnamed: R13.1, U2.3 (QD)
unnamed: R14.4, U2.4 (QE)
unnamed: R14.3, U2.5 (QF)
unnamed: R14.2, U2.6 (QG)
unnamed: U2.9 (QH'), U3.14 (SER)
unnamed: R14.1, U2.7 (QH)
unnamed: R15.1, U3.15 (QA)
unnamed: R15.2, U3.1 (QB)

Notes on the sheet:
Current Limiting Resistor to protect µController pin
UART TX/RX are named w.r.t. ESP32
Must be floating or low during flash
I Only
Piezo Speaker
Pulls pin IO2 low during flash
GPIO Pin References
Only have to shift all 16 bits to dump to SD Card (slow, infrequent) or to reset SPE
ESP32 Remote and Self Reset
IO12 cannot be high during boot
Button for manual reset must be removed before flight
Expanded Digital Outputs
(via Andreas Spiess, https://drive.google.com/file/d/1gbKM7DA7PI7s1-ne_VomcjOrb0bE2TPZ/view?usp=sharing)
Sensors on shift register as part of normal ops (100Hz-1kHz sample rate) Radio, flash on direct lines for speed of access and allowing second core to control RF devices independent of shift register
Status LED

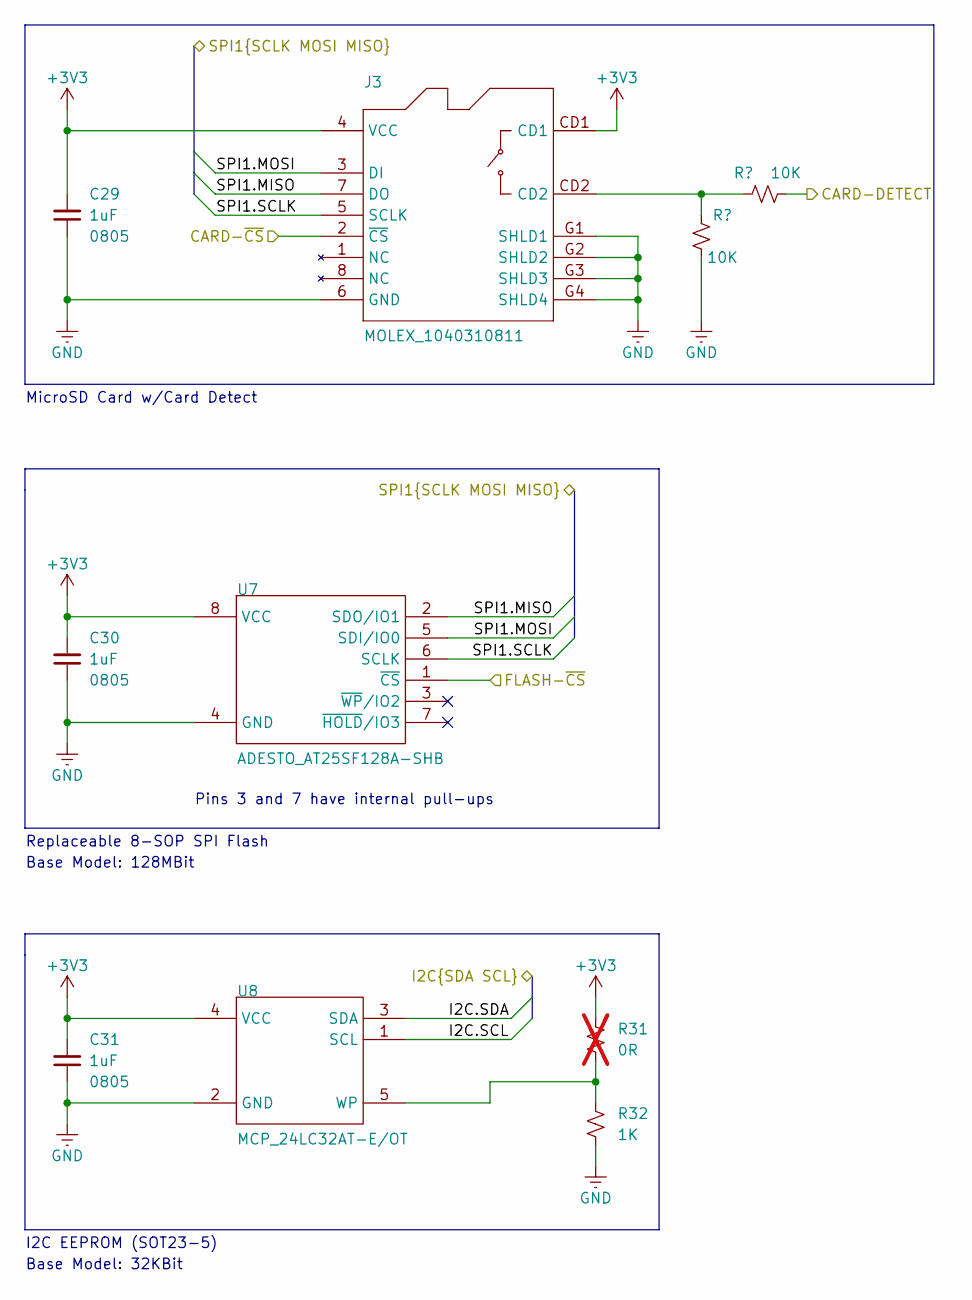
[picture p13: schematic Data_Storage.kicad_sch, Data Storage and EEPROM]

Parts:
C29, C30, C31: 1UF_0805; GENERIC_0805_CAP; Tolerance 10%; Rating 50V
J3: MOLEX_1040310811
R31: 0R_0603; GENERIC_0603_RES; Tolerance 1%; not fitted
R32: 1K_0603; GENERIC_0603_RES; Tolerance 1%
R33, R34: 10K_0603; GENERIC_0603_RES; Tolerance 1%
U7: ADESTO_AT25SF128A-SHB; ADESTO_8S4_(SOP-8)
U8: MCP_24LC32AT-E/OT; MCP_SOT23-5

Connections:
+3V3: C29.2, C30.2, C31.2, J3.4 (VCC), J3.CD1, R31.2, U7.8 (VCC), U8.4 (VCC); also elsewhere on the board
/Data_Storage/CARD-DETECT: R34.2; also elsewhere on the board
/Data_Storage/CARD-~CS: J3.2 (~CS); also elsewhere on the board
/Data_Storage/FLASH-~CS: U7.1 (~CS); also elsewhere on the board
/Data_Storage/I2C.SCL: U8.1 (SCL); also elsewhere on the board
/Data_Storage/I2C.SDA: U8.3 (SDA); also elsewhere on the board
/Data_Storage/SPI1.MISO: J3.7 (DO), U7.2 (SDO/IO1); also elsewhere on the board
/Data_Storage/SPI1.MOSI: J3.3 (DI), U7.5 (SDI/IO0); also elsewhere on the board
/Data_Storage/SPI1.SCLK: J3.5 (SCLK), U7.6 (SCLK); also elsewhere on the board
GND: C29.1, C30.1, C31.1, J3.6 (GND), J3.G1 (SHLD1), J3.G2 (SHLD2), J3.G3 (SHLD3), J3.G4 (SHLD4), R32.1, R33.2, U7.4 (GND), U8.2 (GND); also elsewhere on the board
unnamed: J3.CD2, R33.1, R34.1
unnamed: R31.1, R32.2, U8.5 (WP)

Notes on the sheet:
Pins 3 and 7 have internal pull-ups
MicroSD Card w/Card Detect
I2C EEPROM (SOT23-5)
Base Model: 128MBit
Base Model: 32KBit
Replaceable 8-SOP SPI Flash

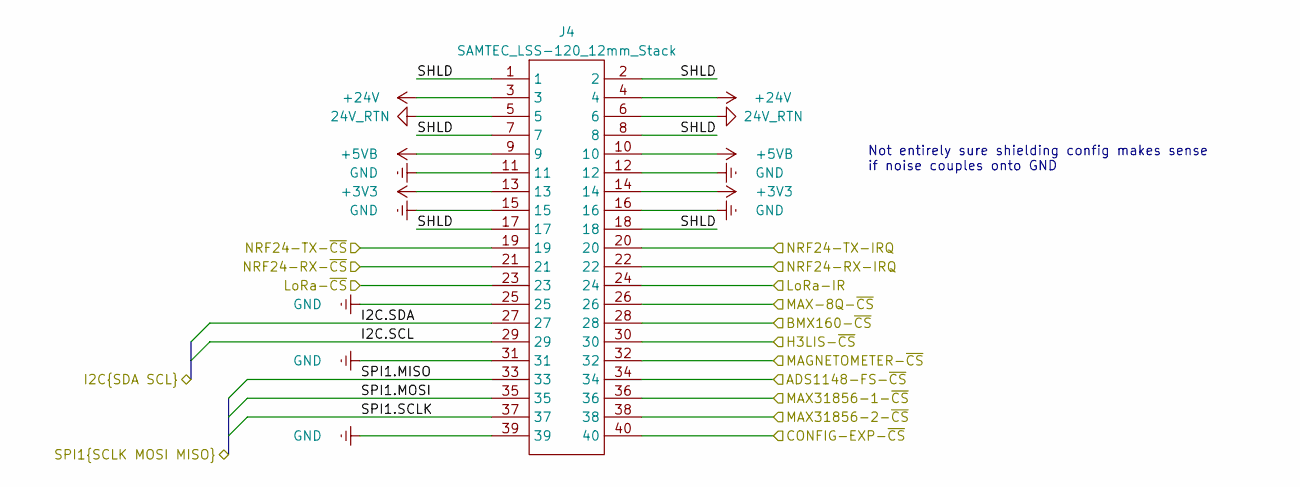
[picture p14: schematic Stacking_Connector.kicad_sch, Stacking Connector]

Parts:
J4: SAMTEC_LSS-120_12mm_Stack

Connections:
24V_RTN: J4.5, J4.6; also elsewhere on the board
+3V3: J4.13, J4.14; also elsewhere on the board
+5VB: J4.9, J4.10; also elsewhere on the board
+24V: J4.3, J4.4; also elsewhere on the board
/Data_Storage/I2C.SCL: J4.29; also elsewhere on the board
/Data_Storage/I2C.SDA: J4.27; also elsewhere on the board
/Data_Storage/SPI1.MISO: J4.33; also elsewhere on the board
/Data_Storage/SPI1.MOSI: J4.35; also elsewhere on the board
/Data_Storage/SPI1.SCLK: J4.37; also elsewhere on the board
/ESP-32_Core/ADS1148-FS-~CS: J4.34; also elsewhere on the board
/ESP-32_Core/BMX160-~CS: J4.28; also elsewhere on the board
/ESP-32_Core/CONFIG-EXP-~CS: J4.40; also elsewhere on the board
/ESP-32_Core/H3LIS-~CS: J4.30; also elsewhere on the board
/ESP-32_Core/LoRa-IR: J4.24; also elsewhere on the board
/ESP-32_Core/LoRa-~CS: J4.23; also elsewhere on the board
/ESP-32_Core/MAGNETOMETER-~CS: J4.32; also elsewhere on the board
/ESP-32_Core/MAX31856-1-~CS: J4.36; also elsewhere on the board
/ESP-32_Core/MAX31856-2-~CS: J4.38; also elsewhere on the board
/ESP-32_Core/MAX-8Q-~CS: J4.26; also elsewhere on the board
/ESP-32_Core/NRF24-RX-IRQ: J4.22; also elsewhere on the board
/ESP-32_Core/NRF24-RX-~CS: J4.21; also elsewhere on the board
/ESP-32_Core/NRF24-TX-IRQ: J4.20; also elsewhere on the board
/ESP-32_Core/NRF24-TX-~CS: J4.19; also elsewhere on the board
/Stacking_Connector/SHLD: J4.1, J4.2, J4.7, J4.8, J4.17, J4.18
GND: J4.11, J4.12, J4.15, J4.16, J4.25, J4.31, J4.39; also elsewhere on the board

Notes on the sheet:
Not entirely sure shielding config makes sense if noise couples onto GND

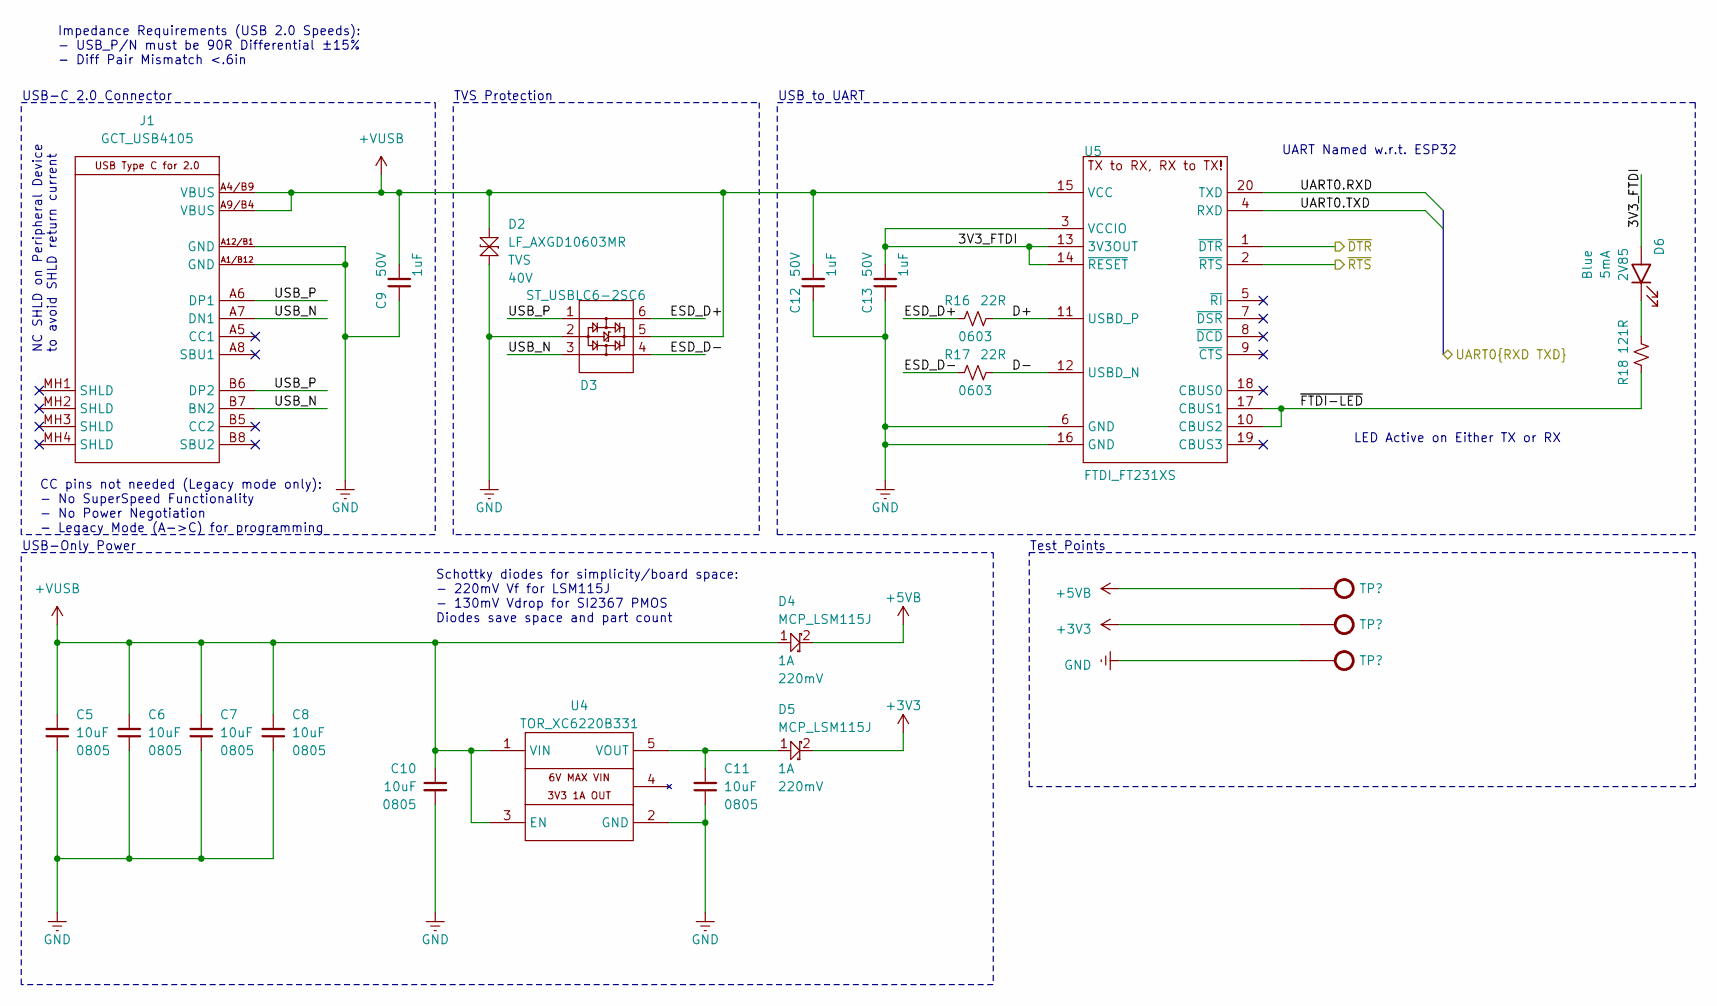
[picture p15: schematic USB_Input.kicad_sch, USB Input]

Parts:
C5, C6, C7, C8, C10, C11: 10UF_0805; GENERIC_0805_CAP; Tolerance 10%; Rating 25V
C9, C12, C13: 1UF_0805; GENERIC_0805_CAP; Tolerance 10%; Rating 50V
D2: LF_AXGD10603MR; LF_AXGD1_0603
D3: ST_USBLC6-2SC6; ST_SOT-23-6L
D4, D5: MCP_LSM115J; MCP_DO-214BA
D6: OSRAM_LBQ39E-N1OO-35-1; OSRAM_0603
J1: GCT_USB4105
R16, R17: 22R_0603; GENERIC_0603_RES; Tolerance 1%
R18: 121R_0603; GENERIC_0603_RES; Tolerance 1%
TP1, TP2, TP3: HARWIN_S1751-46; HARWIN_S1751-XX
U4: TOR_XC6220B331; TOR_SOT-25
U5: FTDI_FT231XS; FTDI_000565_(SSOP-20)

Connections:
+3V3: D5.2, TP2.1; also elsewhere on the board
+5VB: D4.2, TP1.1; also elsewhere on the board
+VUSB: C5.2, C6.2, C7.2, C8.2, C9.2, C10.1, C12.2, D2.2, D3.5 (VBUS), D4.1, J1.A4/B9 (VBUS), J1.A9/B4 (VBUS), U4.1 (VIN), U4.3 (EN), U5.15 (VCC)
/ESP-32_Core/UART0.RXD: U5.20 (TXD); also elsewhere on the board
/ESP-32_Core/UART0.TXD: U5.4 (RXD); also elsewhere on the board
/ESP-32_Core/~DTR: U5.1 (~DTR); also elsewhere on the board
/ESP-32_Core/~RTS: U5.2 (~RTS); also elsewhere on the board
/USB_Input/3V3_FTDI: C13.2, D6.A, U5.3 (VCCIO), U5.13 (3V3OUT), U5.14 (~RESET)
/USB_Input/D+: R16.2, U5.11 (USBD_P)
/USB_Input/D-: R17.2, U5.12 (USBD_N)
/USB_Input/ESD_D+: D3.6 (I01), R16.1
/USB_Input/ESD_D-: D3.4 (I02), R17.1
/USB_Input/USB_N: D3.3 (IO2), J1.A7 (DN1), J1.B7 (BN2)
/USB_Input/USB_P: D3.1 (I01), J1.A6 (DP1), J1.B6 (DP2)
/USB_Input/~FTDI-LED: R18.1, U5.10 (CBUS2), U5.17 (CBUS1)
GND: C5.1, C6.1, C7.1, C8.1, C9.1, C10.2, C11.1, C12.1, C13.1, D2.1, D3.2 (GND), J1.A1/B12 (GND), J1.A12/B1 (GND), TP3.1, U4.2 (GND), U5.6 (GND), U5.16 (GND); also elsewhere on the board
unnamed: D6.C, R18.2
unnamed: C11.2, D5.1, U4.5 (VOUT)

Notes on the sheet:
USB to UART
LED Active on Either TX or RX
CC pins not needed (Legacy mode only): - No SuperSpeed Functionality - No Power Negotiation - Legacy Mode (A->C) for programming
USB-Only Power
NC SHLD on Peripheral Device to avoid SHLD return current
UART Named w.r.t. ESP32
TVS Protection
Schottky diodes for simplicity/board space: - 220mV Vf for LSM115J - 130mV Vdrop for SI2367 PMOS Diodes save space and part count
USB-C 2.0 Connector
Test Points
Impedance Requirements (USB 2.0 Speeds): - USB_P/N must be 90R Differential ±15% - Diff Pair Mismatch <.6in

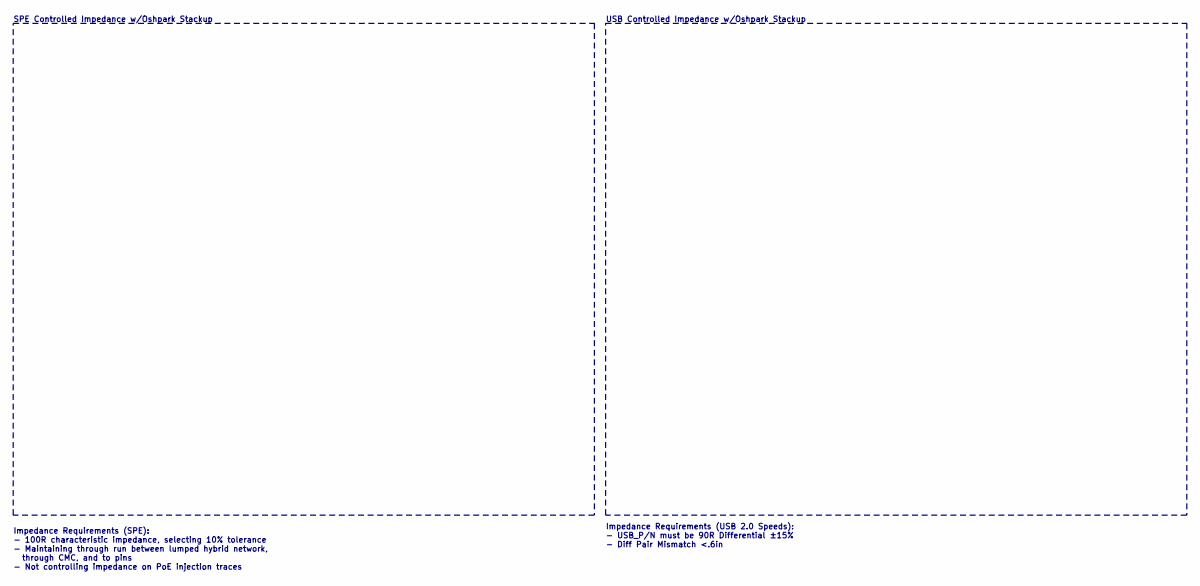
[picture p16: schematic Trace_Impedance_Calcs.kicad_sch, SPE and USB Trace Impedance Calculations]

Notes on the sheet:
Impedance Requirements (USB 2.0 Speeds): - USB_P/N must be 90R Differential ±15% - Diff Pair Mismatch <.6in
SPE Controlled Impedance w/Oshpark Stackup
USB Controlled Impedance w/Oshpark Stackup
Impedance Requirements (SPE): - 100R characteristic impedance, selecting 10% tolerance - Maintaining through run between lumped hybrid network, through CMC, and to pins - Not controlling impedance on PoE injection traces

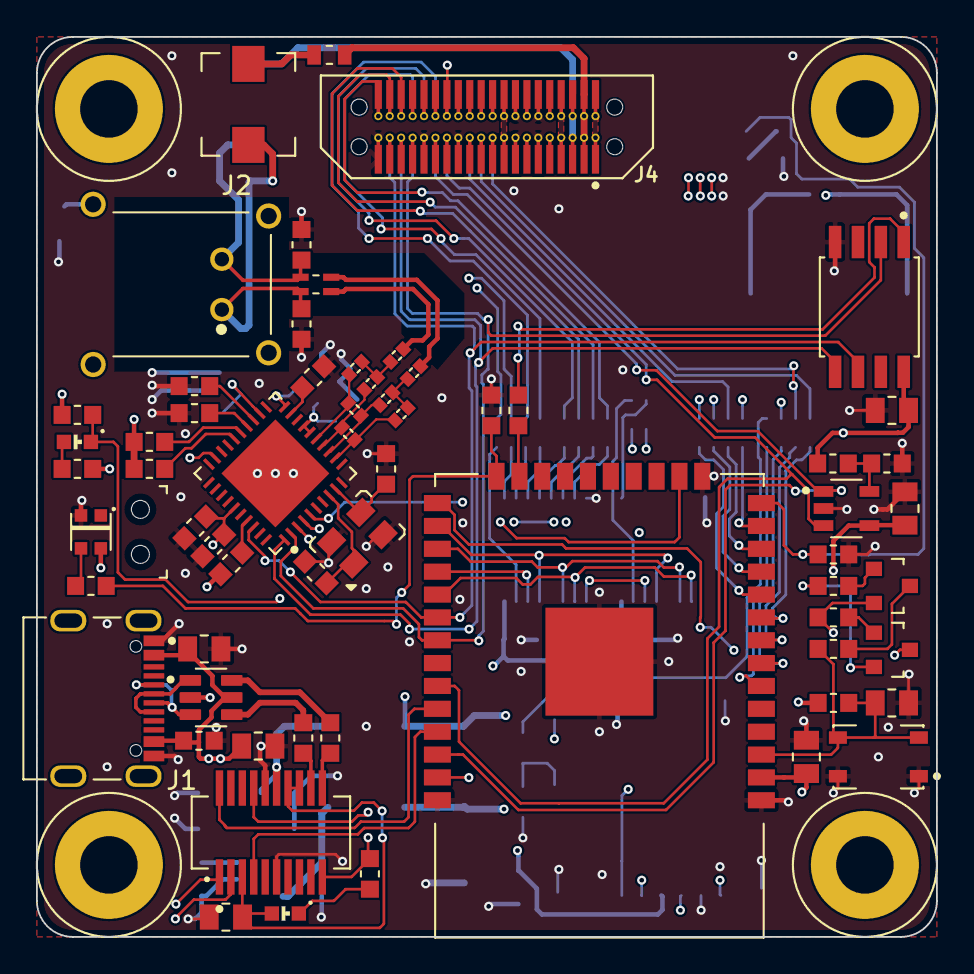
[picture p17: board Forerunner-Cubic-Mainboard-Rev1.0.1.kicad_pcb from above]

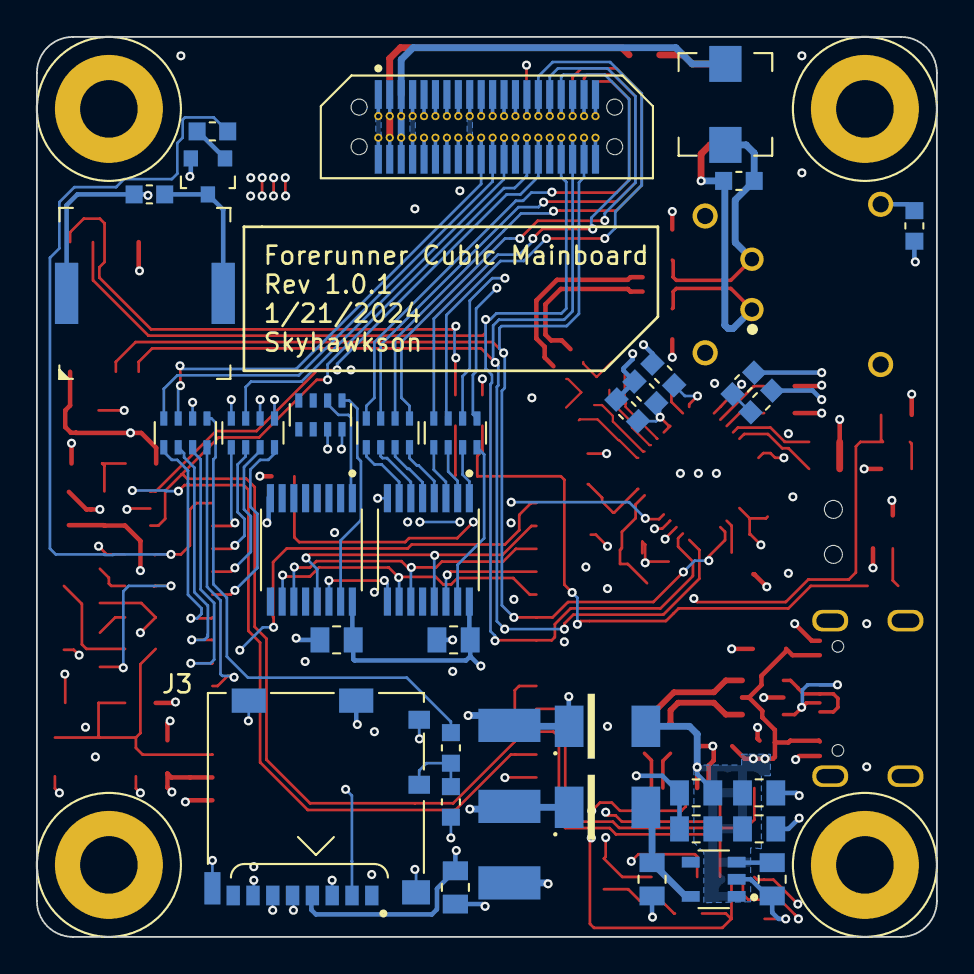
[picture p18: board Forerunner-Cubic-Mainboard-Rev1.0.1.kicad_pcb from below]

Board: 4 copper layers, 50.0 x 50.0 mm, 104 parts (37 on the bottom side), 104 nets.

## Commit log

2024-02-05 Add Rev1.0.1 Release Files
    Added files from Rev1.0.1 Release from another repository
    [Case Bottom.SLDPRT, Case Bottom.STL, Case Top.SLDPRT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]
2024-02-05 Added System-Level Documentation
    [Forerunner_Cubic_ICD.xlsx, Power Calculations.xlsx]
